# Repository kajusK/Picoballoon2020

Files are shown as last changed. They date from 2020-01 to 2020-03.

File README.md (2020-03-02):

Picoballoon Challenge 2020, Deadbadger probe
============================================

This probe was designed [Picoballoon Challenge](https://www.hvezdarna.cz/?p=8167)
organised by Brno Observatory and Planetarium. A goal of this competition
is to make a probe under 20 grams that would be launched on ballon to altitudes
around 5-15 km. Only requirement except weight is sending altitude of the probe.

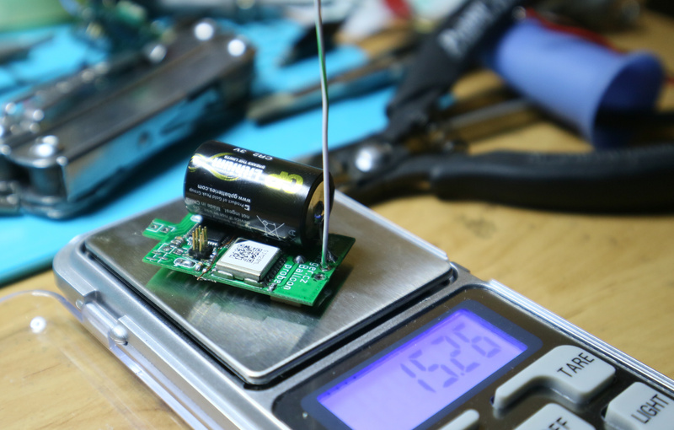
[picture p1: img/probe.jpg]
probe


A detailed description is available at [deadbadger.cz](https://deadbadger.cz/projects/picoballoon-2020),
tracking site is at [bal.deadbadger.cz](https://bal.deadbadger.cz).

The probe contains
  * STM32F030 MCU
  * MS5607 Pressure and temperature sensor
  * Si7020 Relative humidity sensor
  * SIM28ML GPS module
  * RFM95 LoRa Transceiver
  * MCP1640 based solar supercap charger (optinal)
  * 3.3 V boost regulator with 2.7 V startup supervisor

Firmware
--------
As the commonly used [LMIC](https://github.com/matthijskooijman/arduino-lmic/tree/master/src)
library is quite bulky and far from perfect, I wrote my own LoRaWan library
inspired by [TinyLoRa](https://github.com/adafruit/TinyLoRa).

The main loop does about this:
  * Power up, initialize peripherals
  * Power on GPS
  * Measure system voltages, pressure, humidity
  * Wait for GPS data or timeout
  * Power off GPS
  * Send data over LoRa (ABP, unconfirmed uplink)
  * Unlock power latch (keeps probe powered when supercap voltage drops below 2.7 V)
  * Sleep for 30 minutes
  * Repeat (GPS is powered on every 4 cycles)

Hardware
--------
The board was designed for 0.6 mm thick two sided PCB to reduce weight as
much as possible. Using thicker boards (usually 1.6 mm) changes the antenna
trace impedance, but it should not be that significant.

The solar supercap charger can be snapped off if the probe is powered by battery

Frontend
--------
Data received by [TTN](https://www.thethingsnetwork.org/) are sent over
HTTP integration to custom endpoint written in PHP, it verifies the
auth header and stores data in sqlite database.

User frontend is written in PHP, it shows all received packets in table
and generates flight path on a [map](https://api.mapy.cz).

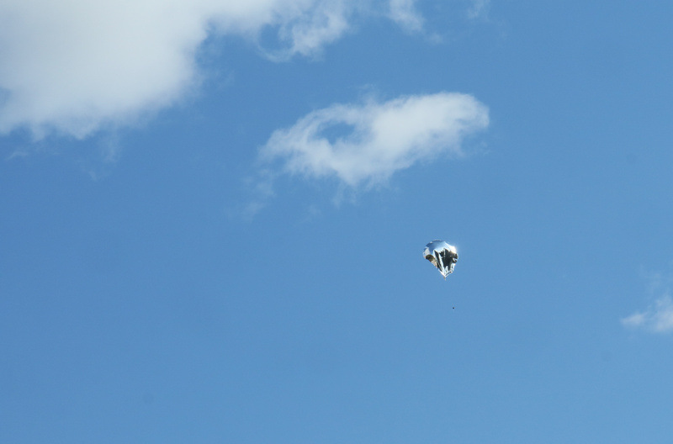
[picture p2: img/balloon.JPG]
balloon


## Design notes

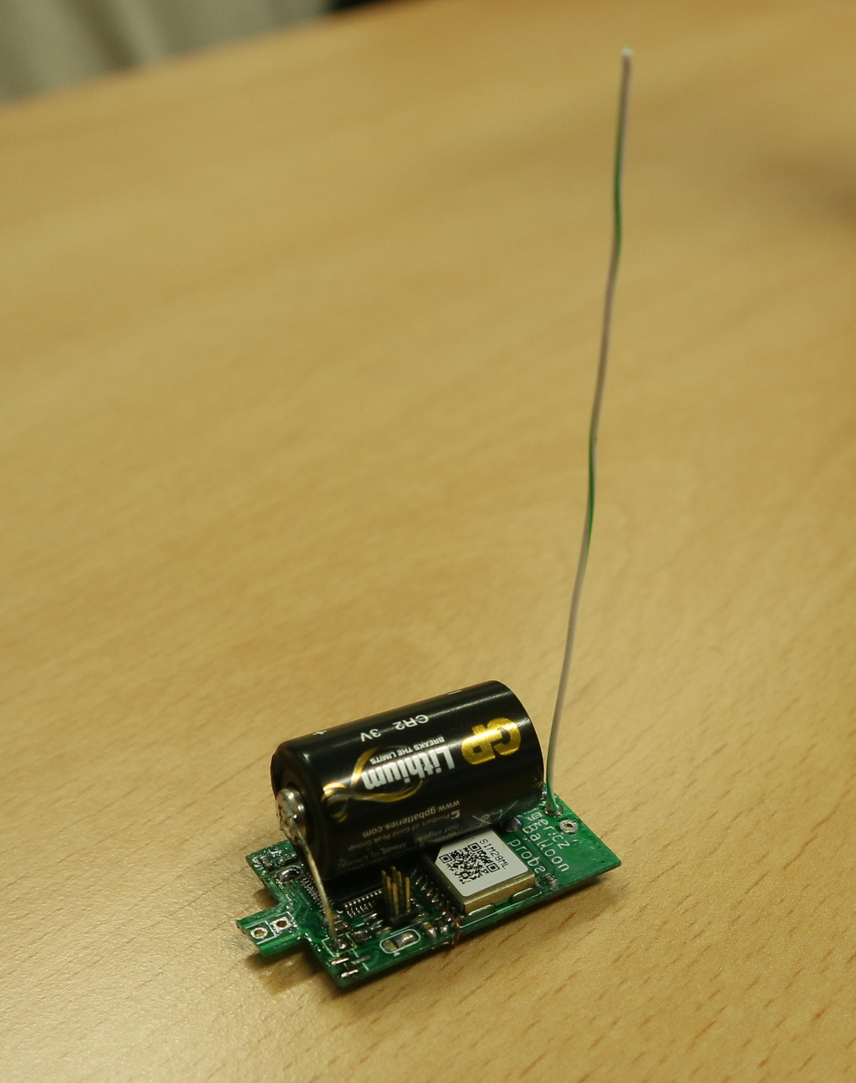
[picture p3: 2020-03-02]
sw/webpage/probe.jpg

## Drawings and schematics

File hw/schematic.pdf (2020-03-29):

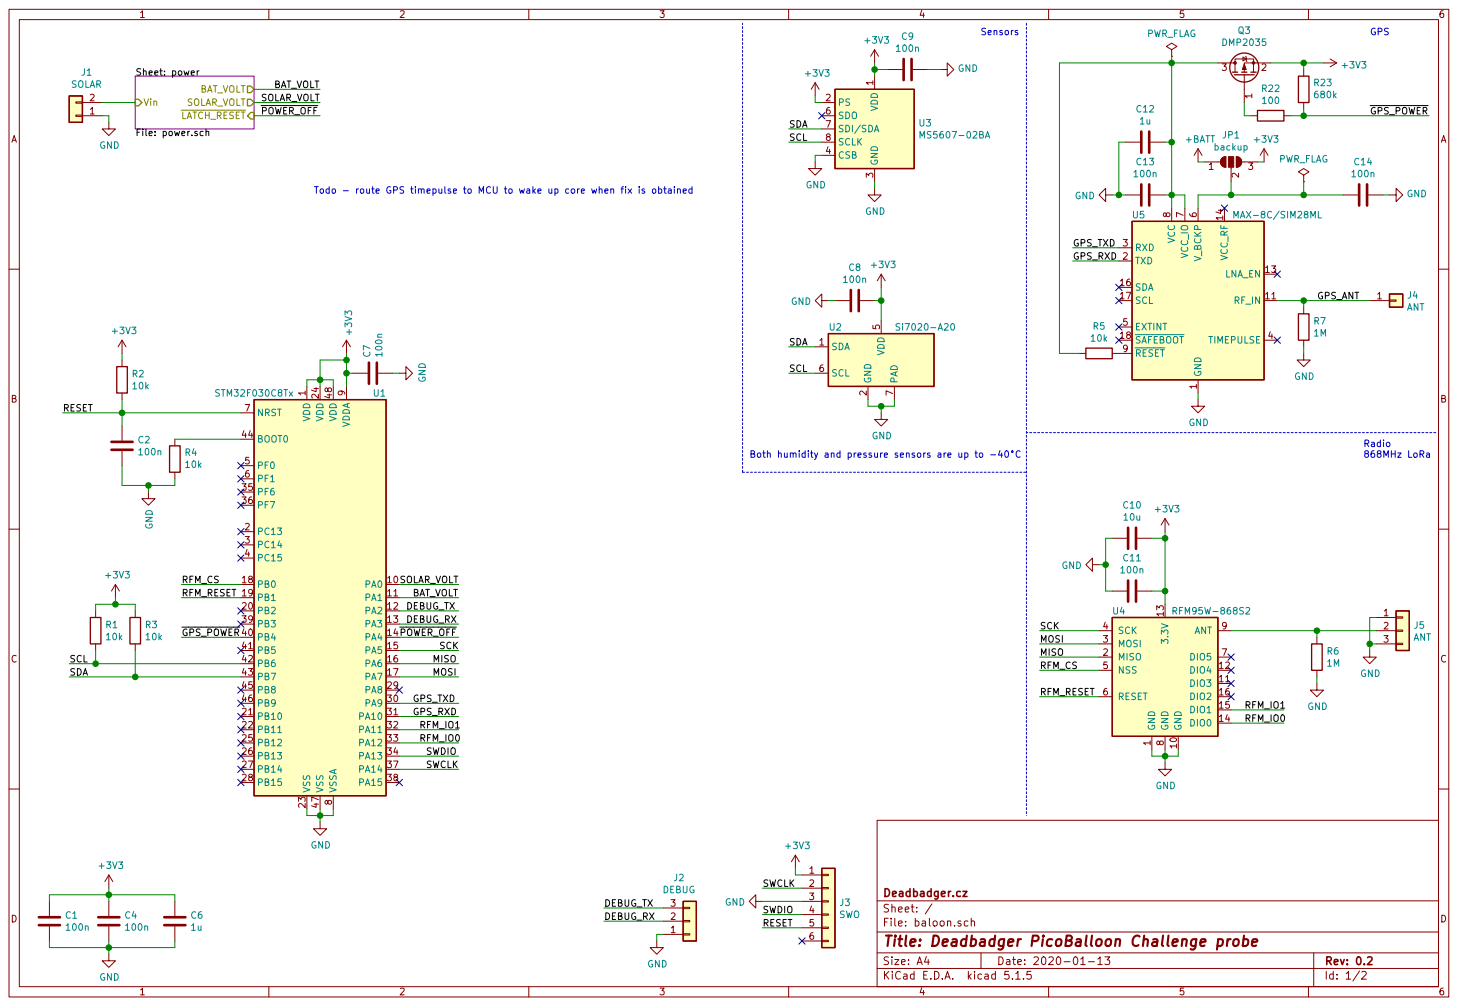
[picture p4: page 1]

3 CSB 4 SDO 6 SDI/SDA 7 SCLK 8 U3MS5607-02BA GND

1 PA0 10 PA1 11 PA2 12 PA3 13 PA4 14 PA5 15 PA6 16 PA7 17 PB0 18 PB1 19 PC13 2 PB2 20 PB10 21 PB11 22 VSS 23 VDD 24 PB12 25 PB13 26 PB14 27 PB15 28 PA8 29 PC14 3 PA9 30 PA10 31 PA11 32 PA12 33 PA13 34 PF6 35 PF7 36 PA14 37 PA15 38 PB3 39 PC15 4 PB4 40 PB5 41 PB6 42 PB7 43 BOOT0 44 PB8 45 PB9 46 VSS 47 VDD 48 PF0 5 PF1 6 NRST 7 VSSA

Both humidity and pressure sensors are up to -40°C

1 GND 10 DIO3 11 DIO4 12 3.3V 13 DIO0 14 DIO1 15 DIO2 16 MISO 2 MOSI 3 SCK 4 NSS 5 RESET 6 DIO5 7 GND

File: baloon.sch Sheet: / Deadbadger.cz

Id: 1/2 Title: Deadbadger PicoBalloon Challenge probe

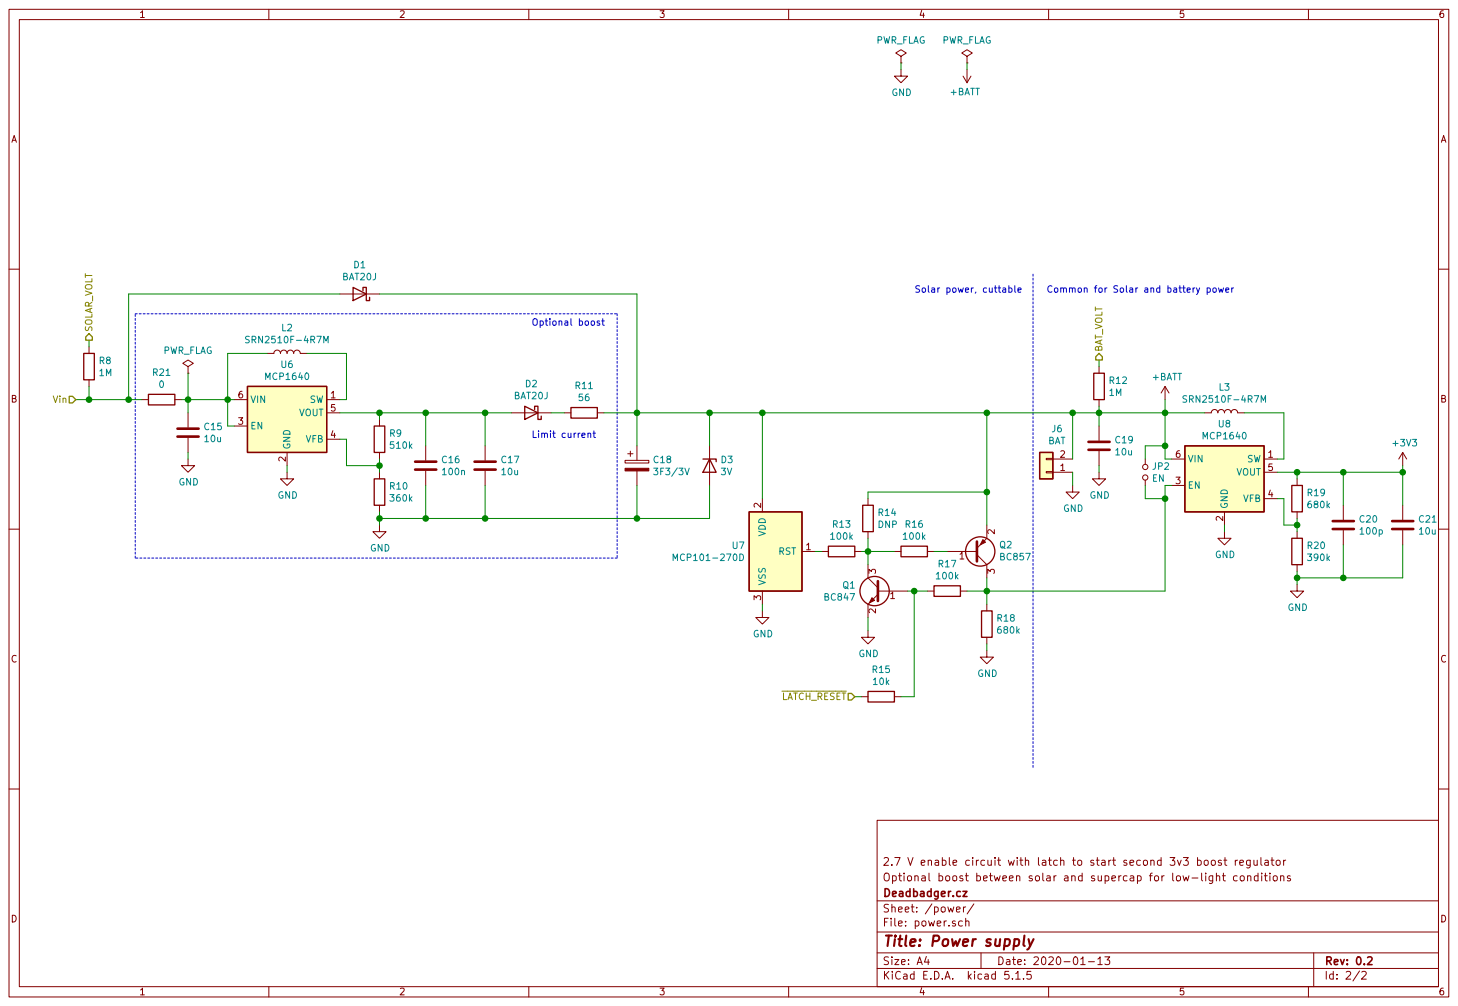
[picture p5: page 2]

2 EN 3 VFB 4 VOUT 5 VIN 6 U6 MCP1640

2 EN 3 VFB 4 VOUT 5 VIN 6 U8 MCP1640 RST 1 VDD

10u GND
2.7 V enable circuit with latch to start second 3v3 boost regulator R10

Optional boost between solar and supercap for low-light conditions
Deadbadger.cz
Sheet: /power/
File: power.sch
Id: 2/2 Title: Power supply

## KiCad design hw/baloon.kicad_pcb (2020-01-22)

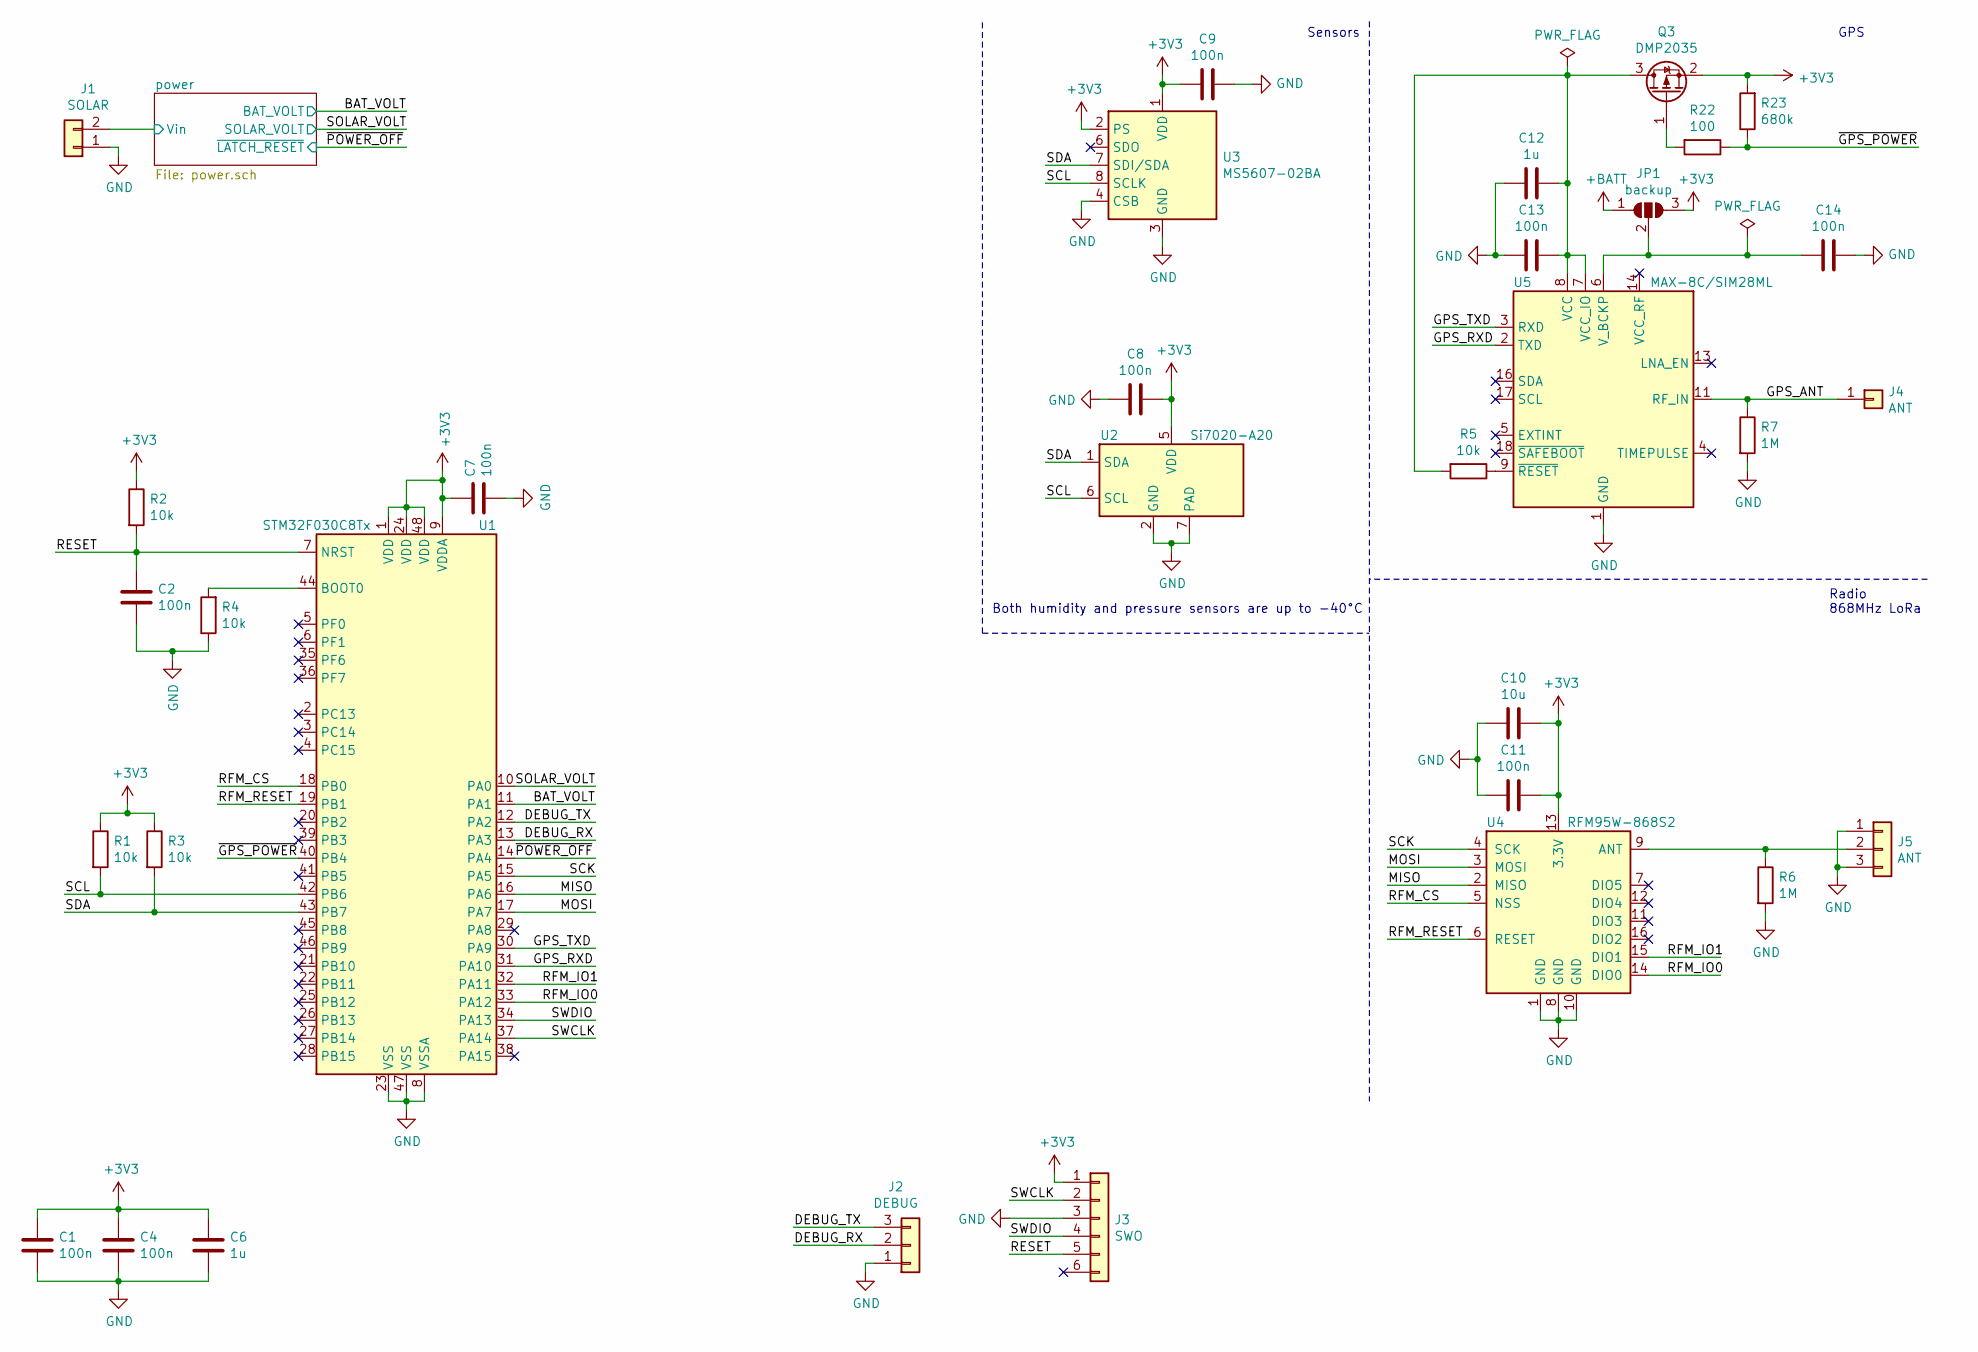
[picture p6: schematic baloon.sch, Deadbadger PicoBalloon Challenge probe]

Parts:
C1, C2, C4, C7, C8, C9, C11, C13, C14: 100n; C_0603_1608Metric
C6, C12: 1u; C_0603_1608Metric
C10: 10u; C_0603_1608Metric
J1: SOLAR; PinHeader_1x02_P2.54mm_Vertical
J2: DEBUG; PinSocket_1x03_P1.00mm_Vertical_SMD_Pin1Left
J3: SWO; PinHeader_2x03_P1.27mm_Vertical_SMD
J4: ANT; SolderWirePad_1x01_Drill1mm
J5: ANT; SolderWirePad_1x03_P3.175mm_Drill0.8mm
JP1: backup; SolderJumper-3_P1.3mm_Open_RoundedPad1.0x1.5mm
Q3: DMP2035; SOT-23
R1, R2, R3, R4, R5: 10k; R_0603_1608Metric
R6, R7: 1M; R_0603_1608Metric
R22: 100; R_0603_1608Metric
R23: 680k; R_0603_1608Metric
U1: STM32F030C8Tx; LQFP-48_7x7mm_P0.5mm
U2: Si7020-A20; DFN-6-1EP_3x3mm_P1mm_EP1.5x2.4mm
U3: MS5607-02BA; LGA-8_3x5mm_P1.25mm
U4: RFM95W-868S2; HOPERF_RFM9XW_SMD
U5: MAX-8C/SIM28ML; ublox_MAX

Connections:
+3V3: C1.1, C4.1, C6.1, C7.1, C8.1, C9.2, C10.1, C11.1, J3.1, JP1.3 (B), Q3.2 (S), R1.1, R2.1, R3.1, R23.2, U1.1 (VDD), U1.9 (VDDA), U1.24 (VDD), U1.48 (VDD), U2.5 (VDD), U3.1 (VDD), U3.2 (PS), U4.13 (3.3V); also elsewhere on the board
+BATT: JP1.1 (A); also elsewhere on the board
/BAT_VOLT: U1.11 (PA1); also elsewhere on the board
/DEBUG_RX: J2.2, U1.13 (PA3)
/DEBUG_TX: J2.3, U1.12 (PA2)
/GPS_ANT: J4.1, R7.1, U5.11 (RF_IN)
/GPS_RXD: U1.31 (PA10), U5.2 (TXD)
/GPS_TXD: U1.30 (PA9), U5.3 (RXD)
/MISO: U1.16 (PA6), U4.2 (MISO)
/MOSI: U1.17 (PA7), U4.3 (MOSI)
/RESET: C2.1, J3.5, R2.2, U1.7 (NRST)
/RFM_CS: U1.18 (PB0), U4.5 (NSS)
/RFM_IO0: U1.33 (PA12), U4.14 (DIO0)
/RFM_IO1: U1.32 (PA11), U4.15 (DIO1)
/RFM_RESET: U1.19 (PB1), U4.6 (RESET)
/SCK: U1.15 (PA5), U4.4 (SCK)
/SCL: R1.2, U1.42 (PB6), U2.6 (SCL), U3.8 (SCLK)
/SDA: R3.2, U1.43 (PB7), U2.1 (SDA), U3.7 (SDI/SDA)
/SOLAR_VOLT: U1.10 (PA0); also elsewhere on the board
/SWCLK: J3.2, U1.37 (PA14)
/SWDIO: J3.4, U1.34 (PA13)
/power/Vin: J1.2; also elsewhere on the board
/~GPS_POWER: R22.1, R23.1, U1.40 (PB4)
/~POWER_OFF: U1.14 (PA4); also elsewhere on the board
GND: C1.2, C2.2, C4.2, C6.2, C7.2, C8.2, C9.1, C10.2, C11.2, C12.2, C13.2, C14.1, J1.1, J2.1, J3.3, J5.1, J5.3, R4.1, R6.2, R7.2, U1.8 (VSSA), U1.23 (VSS), U1.47 (VSS), U2.2 (GND), U2.7 (PAD), U3.3 (GND), U3.4 (CSB), U3.5 (CSB), U4.1 (GND), U4.8 (GND), U4.10 (GND), U5.1 (GND), U5.10 (GND), U5.12 (GND); also elsewhere on the board
unnamed: C12.1, C13.1, Q3.3 (D), R5.2, U5.7 (VCC_IO), U5.8 (VCC)
unnamed: C14.2, JP1.2 (C), U5.6 (V_BCKP)
unnamed: J5.2, R6.1, U4.9 (ANT)
unnamed: Q3.1 (G), R22.2
unnamed: R4.2, U1.44 (BOOT0)
unnamed: R5.1, U5.9 (~RESET)

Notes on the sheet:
Radio 868MHz LoRa
GPS
Sensors
Both humidity and pressure sensors are up to -40°C

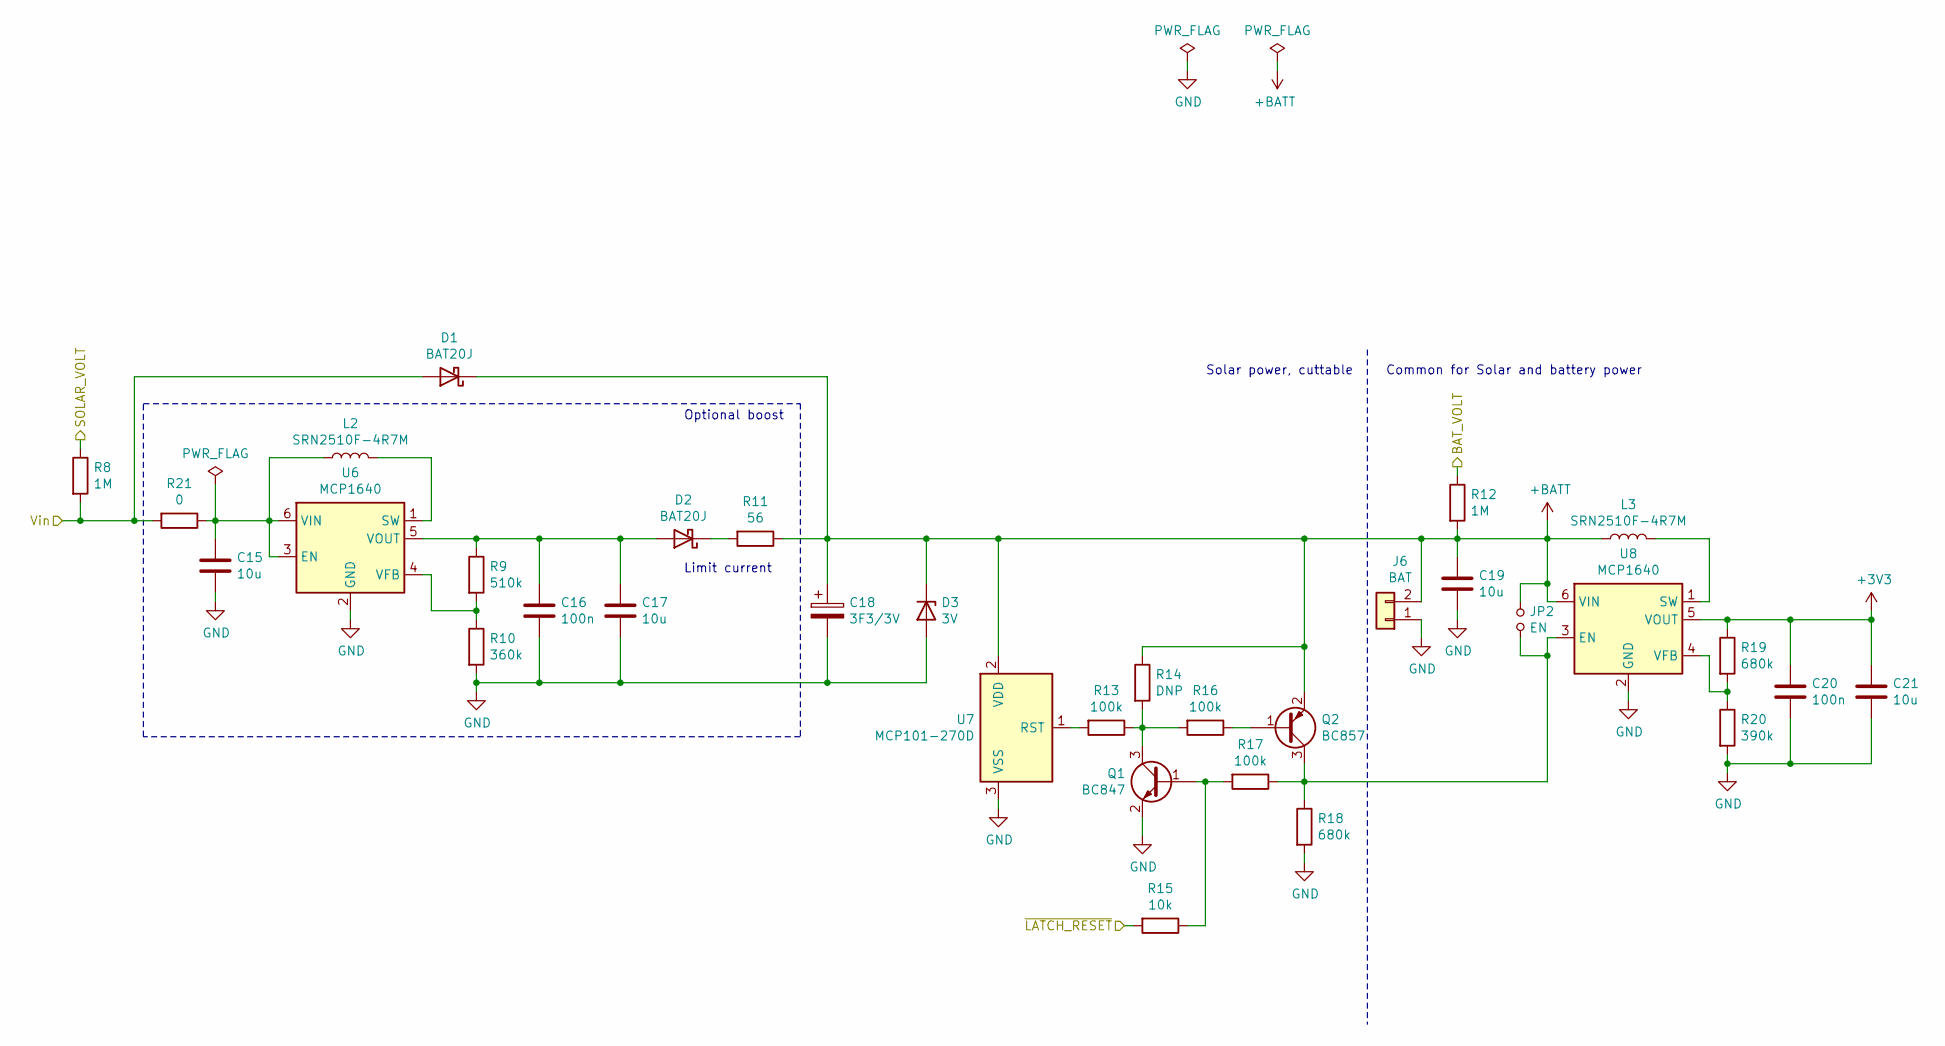
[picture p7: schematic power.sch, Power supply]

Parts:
C15, C17, C19, C21: 10u; C_0603_1608Metric
C16, C20: 100n; C_0603_1608Metric
C18: 3F3/3V; R_LDR_5.2x5.2mm_P3.5mm_Horizontal
D1, D2: BAT20J; D_SOD-323
D3: 3V; D_SOD-323
J6: BAT; PinHeader_1x02_P2.54mm_Vertical
JP2: EN; SolderJumper-2_P1.3mm_Open_RoundedPad1.0x1.5mm
L2, L3: SRN2510F-4R7M; L_Abracon_ASPI-3012S
Q1: BC847; SOT-23
Q2: BC857; SOT-23
R8, R12: 1M; R_0603_1608Metric
R9: 510k; R_0603_1608Metric
R10: 360k; R_0603_1608Metric
R11: 56; R_0603_1608Metric
R13, R16, R17: 100k; R_0603_1608Metric
R14: DNP; R_0603_1608Metric
R15: 10k; R_0603_1608Metric
R18, R19: 680k; R_0603_1608Metric
R20: 390k; R_0603_1608Metric
R21: 0; R_0603_1608Metric
U6, U8: MCP1640; SOT-23-6
U7: MCP101-270D; SOT-23

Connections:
+3V3: C20.1, C21.1, R19.1, U8.5 (VOUT); also elsewhere on the board
+BATT: C18.1, C19.1, D1.1 (K), D3.1 (K), J6.2, JP2.1, L3.1, Q2.2 (E), R11.1, R12.2, R14.1, U7.2 (VDD), U8.6 (VIN); also elsewhere on the board
/BAT_VOLT: R12.1; also elsewhere on the board
/SOLAR_VOLT: R8.1; also elsewhere on the board
/power/Vin: D1.2 (A), R8.2, R21.2; also elsewhere on the board
/~POWER_OFF: R15.2; also elsewhere on the board
GND: C15.2, C16.2, C17.2, C18.2, C19.2, C20.2, C21.2, D3.2 (A), J6.1, Q1.2 (E), R10.2, R18.2, R20.2, U6.2 (GND), U7.3 (VSS), U8.2 (GND); also elsewhere on the board
unnamed: C15.1, L2.1, R21.1, U6.3 (EN), U6.6 (VIN)
unnamed: C16.1, C17.1, D2.2 (A), R9.1, U6.5 (VOUT)
unnamed: D2.1 (K), R11.2
unnamed: JP2.2, Q2.3 (C), R17.1, R18.1, U8.3 (EN)
unnamed: L2.2, U6.1 (SW)
unnamed: L3.2, U8.1 (SW)
unnamed: Q1.1 (B), R15.1, R17.2
unnamed: Q1.3 (C), R13.1, R14.2, R16.2
unnamed: Q2.1 (B), R16.1
unnamed: R9.2, R10.1, U6.4 (VFB)
unnamed: R13.2, U7.1 (RST)
unnamed: R19.2, R20.1, U8.4 (VFB)

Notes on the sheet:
Limit current
Optional boost
Common for Solar and battery power
Solar power, cuttable

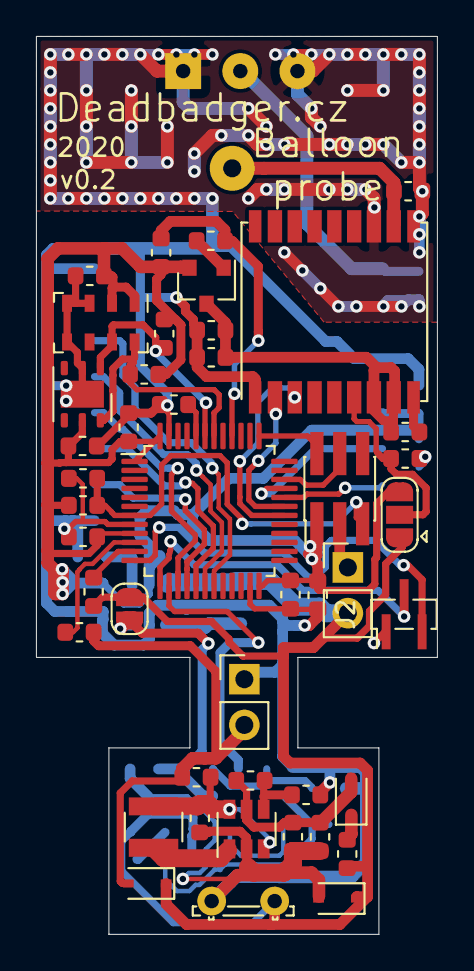
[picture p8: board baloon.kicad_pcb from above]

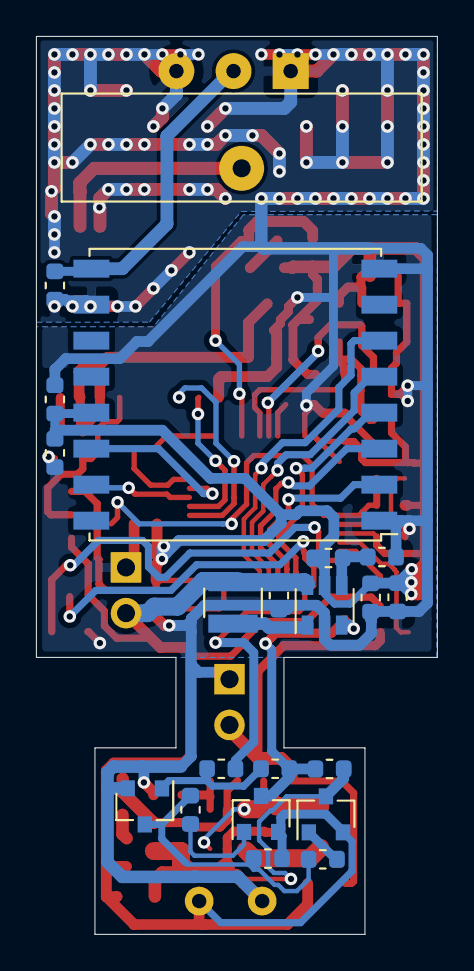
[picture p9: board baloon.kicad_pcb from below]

Board: 2 copper layers, 22.3 x 49.9 mm, 66 parts (20 on the bottom side), 43 nets.

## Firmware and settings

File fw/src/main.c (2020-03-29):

/*
 * Copyright (C) 2020 Jakub Kaderka
 *
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
 * You should have received a copy of the GNU General Public License
 * along with this program.  If not, see <https://www.gnu.org/licenses/>.
 */

/**
 * @file    app/main.c
 * @brief   Main file for deadbadger.cz picoballoon
 *
 * @addtogroup app
 *
 * @{
 */

#include <types.h>

#include <libopencm3/stm32/rcc.h>
#include <libopencm3/stm32/i2c.h>
#include <libopencm3/stm32/spi.h>

#include <hal/io.h>
#include <hal/adc.h>
#include <hal/i2c.h>
#include <hal/spi.h>
#include <hal/uart.h>
#include <hal/rtc.h>
#include <hal/power.h>
#include <hal/flash.h>
#include <utils/time.h>

#include <modules/log.h>
#include <modules/lora.h>
#include <drivers/gps.h>
#include <drivers/ms5607.h>
#include <drivers/si7020.h>
#include <drivers/rfm.h>

#include "config.h"

typedef struct {
    uint8_t gps_power: 1;       /**< GPS power was active during the period */
    uint8_t power_latch: 1;     /**< Power latch is turned off (solar only power */
    uint8_t gps_fix: 1;         /**< Have recent GPS fix */
    uint8_t ms5607_ok: 1;       /**< MS5607 sensor is ok */
    uint8_t si7020_ok: 1;       /**< MS5607 sensor is ok */
} telemetry_bf_t;

typedef struct {
    telemetry_bf_t state;   /** State of the probe outputs,... */
    uint16_t press_daPa;    /** Air pressure in deca Pascals (*10) */
    int16_t temp_dc;        /** Temperature in deci Celsius (/10) */
    int8_t core_temp_c;     /** MCU core temperature in degrees Celsius */
    uint8_t RH;             /** Relative humidity in pct */
    uint16_t alt_m;         /** Altitude in meters */
    float lat;              /** Latitude in decimal degrees */
    float lon;              /** Longitude in decimal degrees */
    uint16_t bat_mv;        /**< Voltage of the battery/supercap */
    uint16_t solar_mv;      /**< Voltage of the solar cell */
    uint8_t loop_time_s;    /**< Time since wake up until packet creation */
} __attribute__((packed)) telemetry_packet_t;

/** The Thing Network auth data */
static const uint8_t ttn_DevAddr[16] = TTN_DEV_ADDR;
static const uint8_t ttn_NwkSkey[16] = TTN_NWKSKEY;
static const uint8_t ttn_AppSkey[16] = TTN_APPSKEY;

/** Address to store Lora counter value, first address, align to page boundary */
#define LORA_TX_COUNTER_ADDR0 0xF000

/**
 * Address to store Lora counter value, second address (offseted by smallest
 * erasable area from previous one
 */
#define LORA_TX_COUNTER_ADDR1 (LORA_TX_COUNTER_ADDR0 + FLASHD_PAGE_SIZE)

/**
 * Control GPS power switch
 *
 * @param on    True to power on, false to power off
 */
static void App_GpsPower(bool on)
{
    IOd_SetLine(LINE_GPS_POWER_N, !on);
}

/**
 * Disable latch on power supply (if supercap voltage is low, power off)
 *
 * @param disable   True to disable
 */
static void App_LatchDisable(bool disable)
{
    IOd_SetLine(LINE_POWER_OFF_N, !disable);
}

/**
 * Set LoRa region based on recent known location
 *
 * @param gps_lat   Latitude
 * @param gps_lon   Longitude
 */
static void App_SetRegion(nmea_float_t gps_lat,
        nmea_float_t gps_lon)
{
    rfm_lora_region_t region = RFM_REGION_EU863;
    int16_t lat = gps_lat.num / gps_lat.scale;
    int16_t lon = gps_lon.num / gps_lon.scale;

    /* America */
    if (lon > -170 && lon < 50) {
        region = RFM_REGION_US902;
    /* Australia, New Zealand */
    } else if  (lat > -50 && lat < -7 && lon > 100 && lon < 170) {
        region = RFM_REGION_AU915;
    /* Japan, Malaysia, etc. */
    } else if (lon > 78 && lon < 160) {
        region = RFM_REGION_AS920;
    }

    RFM_SetLoraRegion(region);
}

/**
 * Save value of the LoRaWan tx counter to internal flash memory
 *
 * @param counter   Counter value
 */
static void App_SaveTxCounter(uint32_t counter)
{
    uint32_t cnt1 = *((uint32_t *) LORA_TX_COUNTER_ADDR0);
    uint32_t cnt2 = *((uint32_t *) LORA_TX_COUNTER_ADDR1);
    uint32_t addr;

    if (cnt1 == (uint32_t) -1) {
        addr = LORA_TX_COUNTER_ADDR0;
    } else if (cnt2 == (uint32_t) -1) {
        addr = LORA_TX_COUNTER_ADDR1;
    } else if (cnt1 > cnt2) {
        addr = LORA_TX_COUNTER_ADDR1;
    } else {
        addr = LORA_TX_COUNTER_ADDR0;
    }
    Flashd_WriteEnable();
    Flashd_ErasePage(addr);
    Flashd_Write(addr, (uint8_t *)&counter, sizeof(counter));
    Flashd_WriteDisable();
}

/**
 * Load saved value of the LoRaWan tx counter
 *
 * @return Saved counter value or 0
 */
static uint32_t App_LoadTxCounter(void)
{
    uint32_t cnt1 = *((uint32_t *) LORA_TX_COUNTER_ADDR0);
    uint32_t cnt2 = *((uint32_t *) LORA_TX_COUNTER_ADDR1);

    if (cnt1 == (uint32_t) -1) {
        if (cnt2 == (uint32_t) -1) {
            return 0;
        }
    }

    if (cnt2 == (uint32_t) -1) {
        return cnt1;
    }

    if (cnt1 > cnt2) {
        return cnt1;
    }
    return cnt2;
}

static void App_Loop(void)
{
    static uint8_t gps_skip = 0;
    telemetry_packet_t packet = {0};
    gps_info_t *gps;
    int32_t temp_mdeg = 0;
    uint32_t press_Pa = 0;
    uint32_t start_ts = millis();
    uint32_t tx_counter;

    Log_Info(NULL, "Measuring");

    packet.bat_mv = Adcd_ReadMv(CHN_BAT_VOLT);
    packet.solar_mv = Adcd_ReadMv(CHN_SOLAR_VOLT);
    packet.core_temp_c = Adcd_ReadTempDegC();
    Adcd_Sleep();

    //not fitted this year
    //packet.RH = SI7020_RH();
    //packet.state.si7020_ok = packet.RH != 0;

    packet.state.ms5607_ok = MS5607_Read(MS5607_OSR1024, &press_Pa, &temp_mdeg);
    packet.press_daPa = press_Pa / 10;
    packet.temp_dc = temp_mdeg / 100;
//    packet.state.gps_power = !IOd_GetLine(LINE_GPS_POWER_N);
//    packet.state.power_latch = !IOd_GetLine(LINE_POWER_OFF_N);

    /* wait for fix */
    while (Gps_Loop() == NULL && (millis() - start_ts) < GPS_FIX_TIMEOUT_S*1000) {
        ;
    }
    gps = Gps_Get();
    if (gps != NULL) {
        App_SetRegion(gps->lat, gps->lon);
        packet.alt_m = gps->altitude_dm/10;
        packet.lat = ((float) gps->lat.num) / gps->lat.scale;
        packet.lon = ((float) gps->lon.num) / gps->lon.scale;
        packet.state.gps_fix = true;
    } else {
        /* keep region from previous fix */
        packet.alt_m = 0;
        packet.lat = 0;
        packet.lon = 0;
        packet.state.gps_fix = false;
    }
    packet.loop_time_s = (millis() - start_ts) / 1000;

    Log_Info(NULL, "Sending data");
    /* Save lora tx counter + 1 (in case, power dies before saving */
    tx_counter = App_LoadTxCounter();
    Lora_SetCounters(0, tx_counter);
    App_SaveTxCounter(tx_counter+1);
    if (!Lora_Send((uint8_t *) &packet, sizeof(packet))) {
        Log_Error(NULL, "Failed to send data over LoRaWan!");
    }
    App_LatchDisable(true);
}

int main(void)
{
    struct tm tm;

    /* Initialize clock system, IO pins and systick */
    IOd_Init();
    Time_Init();

    /* Enable GPS now to get fix ASAP, for now, also rfm95 is wired here */
    App_GpsPower(true);

    /* early init - debug output */
    UARTd_Init(USART_DEBUG_TX, 115200);
    Log_Info(NULL, "PicoBalloon Challenge 2020");
    Log_Info(NULL, "Deadbadger.cz");

    I2Cd_Init(1, false);
    SPId_Init(1, SPID_PRESC_2, SPI_MODE_0);
    UARTd_Init(USART_GPS_TX, 9600);
    RTCd_Init(false);
    Adcd_Init();

    Gps_Init();
    if (!MS5607_Init()) {
        Log_Error(NULL, "MS5607 pressure sensor not responding");
    }
    /*
    if (!SI7020_Init()) {
        Log_Error(NULL, "SI7020 humidity sensor not responding");
    }
    */
    if (!RFM_LoraInit()) {
        Log_Error(NULL, "RFM module not responding!");
    }
    Lora_InitAbp(RFM_LoraSend, ttn_DevAddr, ttn_NwkSkey, ttn_AppSkey);
    RFM_SetLoraRegion(RFM_REGION_EU863);
    RFM_SetLoraParams(RFM_BW_125k, RFM_SF_10);
    RFM_SetPowerDBm(17);

    Log_Info(NULL, "System initialized, running main loop");
    Log_SetLevel(LOG_ERROR);

    /* ================ TODO ================ */
    /* debugging purposes only, remove for production */
    Log_SetLevel(LOG_DEBUG);
    /* ================ TODO ================ */
    while (1) {
        App_Loop();
        App_GpsPower(false);
        /* Don't have wakeup timer, use alarm, only hour, min, sec used */
        RTCd_GetTime(&tm);
        /*
        tm.tm_sec += 10;
        if (tm.tm_sec >= 60) {
            tm.tm_sec %= 60;
            tm.tm_min += 1;
        }
        if (tm.tm_min >= 60) {
            tm.tm_min = 0;
            tm.tm_hour += 1;
            tm.tm_hour %= 24;
        }
        */
        Log_Info(NULL, "Start at %d %d", tm.tm_hour, tm.tm_min);
        if (tm.tm_min + (TELEMETRY_PERIOD_MIN % 60) >= 60) {
            tm.tm_hour += 1;
        }
        tm.tm_hour = (tm.tm_hour + TELEMETRY_PERIOD_MIN / 60) % 24;
        tm.tm_min = (tm.tm_min + TELEMETRY_PERIOD_MIN) % 60;
        Log_Info(NULL, "Start at %d %d", tm.tm_hour, tm.tm_min);

        Log_Info(NULL, "Sleeping for %d minutes", TELEMETRY_PERIOD_MIN);
        RTCd_SetAlarm(&tm, NULL);
        Powerd_Off();
        Log_Error(NULL, "Failed to sleep");
        Powerd_Reboot();
    }
}

/** @} */

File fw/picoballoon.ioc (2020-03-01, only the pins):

Mcu.UserName=STM32F030C8Tx
PA0.GPIO_Label=SOLAR_VOLT
PA0.Signal=ADC_IN0
PA1.GPIO_Label=BAT_VOLT
PA1.Signal=ADC_IN1
PA10.GPIO_Label=GPS_RX
PA10.Signal=USART1_RX
PA11.GPIO_Label=RFM_IO0
PA11.Signal=GPIO_Input
PA12.GPIO_Label=RFM_IO1
PA12.Signal=GPIO_Input
PA13.Signal=SYS_SWDIO
PA14.Signal=SYS_SWCLK
PA2.GPIO_Label=DEBUG_TX
PA2.Signal=USART2_TX
PA3.GPIO_Label=DEBUG_RX
PA3.Signal=USART2_RX
PA4.GPIO_Label=POWER_OFF_N
PA4.Signal=GPIO_Output
PA5.Signal=SPI1_SCK
PA6.Signal=SPI1_MISO
PA7.Signal=SPI1_MOSI
PA9.GPIO_Label=GPS_TX
PA9.Signal=USART1_TX
PB0.GPIO_Label=RFM_CS
PB0.Signal=GPIO_Output
PB1.GPIO_Label=RFM_RESET
PB1.Signal=GPIO_Output
PB4.GPIO_Label=GPS_POWER_N
PB4.Signal=GPIO_Output
PB6.Signal=I2C1_SCL
PB7.Signal=I2C1_SDA

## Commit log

2020-01-22 Final board
    [baloon.kicad_pcb, baloon.sch, power.sch]
2020-01-29 Added power control
2020-01-29 Added extended interrupts control
2020-01-29 Enable both interrupt and event for exti
2020-01-29 Added alarm support, cleared up the rtc driver
2020-02-17 Added pressure sensor driver
2020-02-17 Added SI7020 driver
2020-02-21 Updated core temp measuring variable (+-128 should be enough for temperatures)
2020-02-21 Added invalidate and fix timestamp to gps driver
2020-02-21 Added rfm module driver
2020-02-21 Added probe logic
2020-02-29 Fixed rfm transmit command, regenerated lora frequencies by script
    [lora_freq_gen.py]
2020-02-29 Added timeouts to infinite wait loops in i2c,...
2020-02-29 Clear flags before running i2c transaction
2020-03-01 Fixed nmea parser on arm - va_list seems not to be a pointer, first argument was used in every call as the ap was copied, not accessed as pointer
2020-03-01 Fixed RTC hal driver
2020-03-01 Fixed reading temperature from ms5607
2020-03-01 Keep gps powered off by default
2020-03-02 Show lora position if gps not available, calculate altitude from pressure
2020-03-29 Added schematic
2020-03-29 Hotfixes shortly before launch
    [baloon.sch, power.sch]

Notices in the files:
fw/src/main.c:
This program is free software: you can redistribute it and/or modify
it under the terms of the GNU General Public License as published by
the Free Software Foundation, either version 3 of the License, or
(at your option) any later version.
